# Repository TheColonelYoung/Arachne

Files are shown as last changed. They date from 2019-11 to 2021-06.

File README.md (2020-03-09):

# Project Arachne  
Mainly 3D printed manipulator with 6 axis of freedom based on design of steward platform  

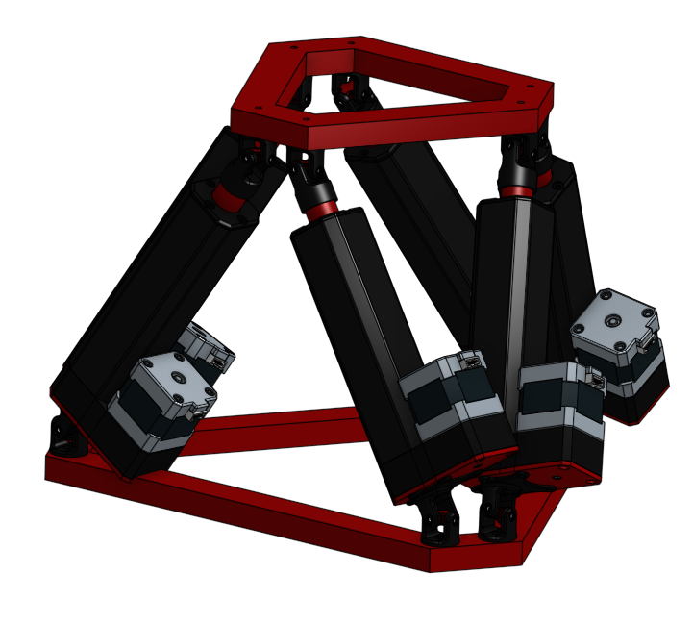
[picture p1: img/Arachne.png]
  

**!!! Now the notes in this repository are rather assumptions that will need to be verified in practice !!!**  

Platform is based on two nearly triangular bases connected with 6 linear actuators.  
Control of these actuators is driven from motherboard.  
Lower base is stationary, upper base part is movable.  
Motherboard is positioned in lower triangle base. Motherboard communicates with controller (pc) via serial line with G-code.  
First version of platform is 3D printed. Next version are supposed to be from aluminium.  

# **Motion system**  
Motion system is based on [affine transformation](https://en.wikipedia.org/wiki/Affine_transformation).  
Basic system contains from seven points. Which are placed in center of platform and in points of connection with actuators.  
Points are on both triangular bases. Corresponding points have same numbers.  
Position of point is described as coordinates in cartesian system.  
Center point is not used for calculation of motion, is used only as center point of mass.  
- Represent zero-point in three-dimensional space  
- Zero point of Z is when platform is set to minimal height (home position)  
- Can probably be used for optimization of speed  
- Center point can be used to determinate unreachable positions (not all) and as center position of object for affine transformations  

Every point is represented as vector [x,y,z,1].  

### Travel distance  
Distance between connect points &nbsp;of actuator on lower and upper bases is calculated.  
- Calculation is based on usage of euclidian distance calculation in three dimensional space  
- $d(a,b) = \sqrt{(a_x - b_x)^2 + (a_y - b_y)^2 + (a_z - b_z)^2}$  

Affine transformation is applied on all point of connection with actuators on upper base.  
Now is calculated new distance between fixed and movable points. Difference between distances in old and new position is travel distance of actuator.  
By repeating this process for every actuator is calculated one move of platform.  
Rotation terms: Pitch(X), Roll(Y), Yaw(Z)  

### Speed  
Speed scaling is linear based on travel distance of actuator.  
Acceleration must grow proportionally as speed.  
Traveled distance is integration of actual speed of motor by time.  
Example: Two motor M1 - travels 10mm, M2 - travels 30mm,  
- Maximal speed is tested (before usage of device) and used for motor with the longest distance (as well as acceleration)  
- M1 use three-times lower speed and acceleration because of travel distance is three-times lower  
- Travel time is same for both motor, so motors cannot jam due to incorrect position  

### Problems  
Jams of platforms are possible when movement is not synchronized. In this state some motor can be in end-position, but motion is not done.  
Main issue is when position of points in unknown. This happens when platform is powered on. Before power of platform must be homed -> this cannot be reliably secured.  
Possible homing sequence is that all actuators will be moved with same speed to their home position. But there is possibility of jam.  

### Example  
This example is calculated only for one actuators, others have same calculations.  
Platform is now at home position. So position of points describes offset from zero point.  
Length of all actuator is same. Probably zero length of pushrods + length of body.  
In this example is body length two times retractable length. Minimal length 30mm, maximal length is 50mm.  
Length is calculated between mates connecting base and actuator.  

Point on upper base ($P_{UP}$) is at `[-2, 0, 0, 1]`, motions are shift forward (Y+2), and rotation to right(Z+90°).  
Point on lower base ($P_{LOW}$) is at `[-1, 2, -2.45, 1]`, Z offset is determinated by vertical distance between lower and upper base in home state.  

**Shift matrix:**  
$\begin{bmatrix}1 & 0 & 0 & X \\0 & 1 & 0 & Y \\ 0 & 0 & 1 & Z \\ 0 & 0 & 0 & 1 \\\end{bmatrix}$  

**Rotation matrix around Z - Yaw($\gamma$):**  
$\begin{bmatrix}\cos(\gamma) & -\sin(\gamma) & 0 & 0 \\\sin(\gamma) & \cos(\gamma) & 0 & 0 \\ 0 & 0 & 1 & 0 \\ 0 & 0 & 0 & 1 \\\end{bmatrix}$  

**Multiplication of matrix**  
Note: if platform is not home is necessary to make another translation of object from current position of center point to center of space. This is represented as empty translation-1 matrix  
[Translation-1 * Rotation * Translation * Point]  

New coordinates of $P_{UP}$ are `[-2, -2, 0, 1]`  

Old distance between $P_{UP}$ and $P_{LOW}$ is: 3.317 cm  
- Calculation: $d = \sqrt{(-2 - -1)^2 + (0 - 2)^2 + (0 - -2.45)^2} = 3.317$  

New distance between $P_{UP}$ and $P_{LOW}$ is: 4.796 cm  
- Calculation: $d = \sqrt{(-2 - -1)^2 + (-2 - 2)^2 + (0 - -2.45)^2} = 4.796$  

Difference between old and new length of actuator is: 1.479 cm  

So actuator must change length to 4.796 cm, which is nearly maximal length (in this example).  
Change of length is + 1.479 cm, speed and acceleration depends on motion of other actuators.  

# **Construction**  

### Joints  
Linear actuators are connected with hexagonal platform with universal joint with can give joint freedom to move freely. Rotation of joint should not be constrained by joint but by length of arm (linear actuator length).  

Joints consists of 3 parts. Two forks and one central block. X and Y axis of forks are perpendicular between forks (forks are turned against self by 90° on Z axis). Fork is connected to central block through small ball bearing. This ball bearing removed as much of friction as possible.  

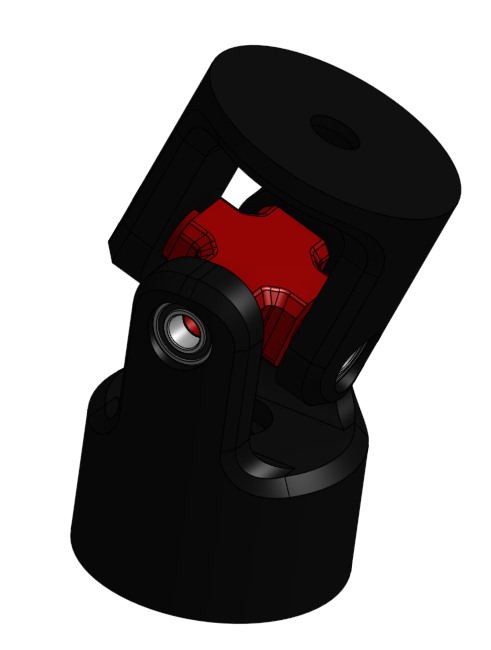
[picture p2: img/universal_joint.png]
Universal joint
  
**Universal joint**  

# **PCB**  
Main Motherboard contains six stepper motor drivers L6470 in TSSOP28 package.  
PCB is designed with maximal dimensions of 10x7cm, so it can be cheaply manufactured.  

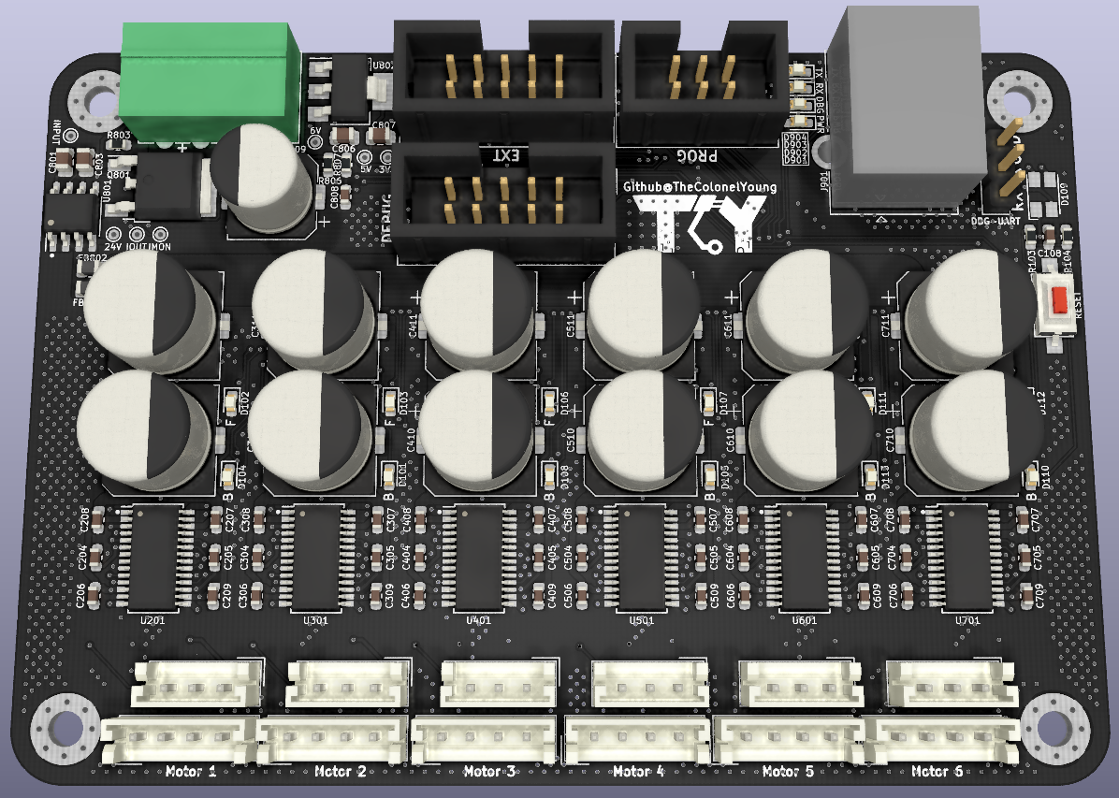
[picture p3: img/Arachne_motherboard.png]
  

### Specifications  
- Maximal input voltage is 36V  
- PCB is designed for maximal current of 8A into motor, this assumes 6x1.2A stepper motors  
- Input stage contains current sensor for monitoring of actual current  
- Stepper motor end position can be detected via driver build-in stall detection or through endstop (one per each stepper)  
    - Endstop should be Normally Open and connect ground to sense pin  
    - Connector contains 3.3V power output for powering some position sensor instead of tactile switch between sense and ground  
- Stepper drivers are in line, so heatsinks can be fit on them  
- Via EXT IDC connector can be connected sensor for motion feedback over SPI or I2C  
- DEBUG connector pinout is compatible with 10-pin IDC Saleae layout  
- Minimal width trace is 5.1 mils (0.13 mm)  
- Minimal drill size id 0.3mm

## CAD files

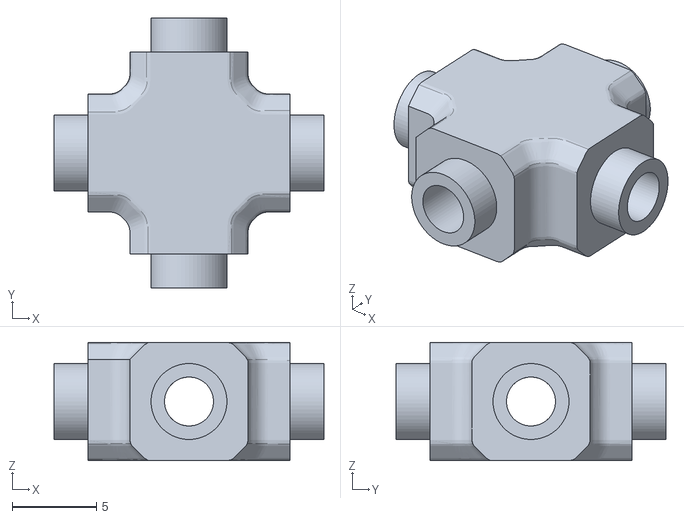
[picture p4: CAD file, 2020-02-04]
STL/Center_block.stl
16.0 x 16.0 x 7.00

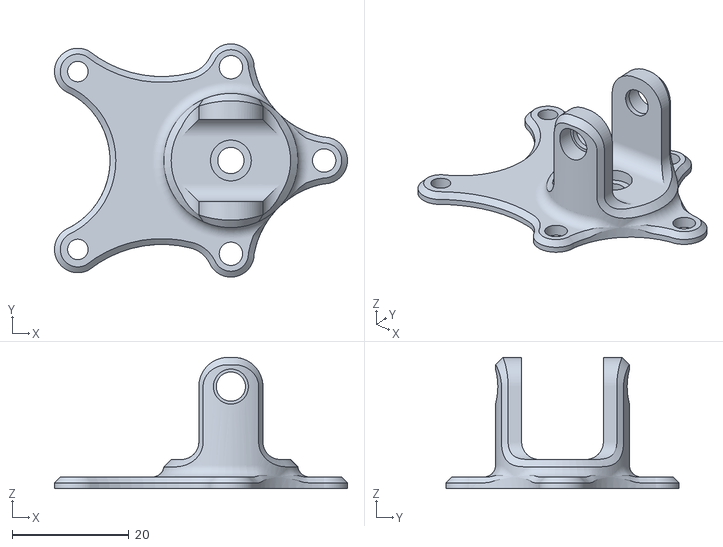
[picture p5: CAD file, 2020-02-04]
STL/Joint_fork_gearbox.stl
50.2 x 40.0 x 22.5

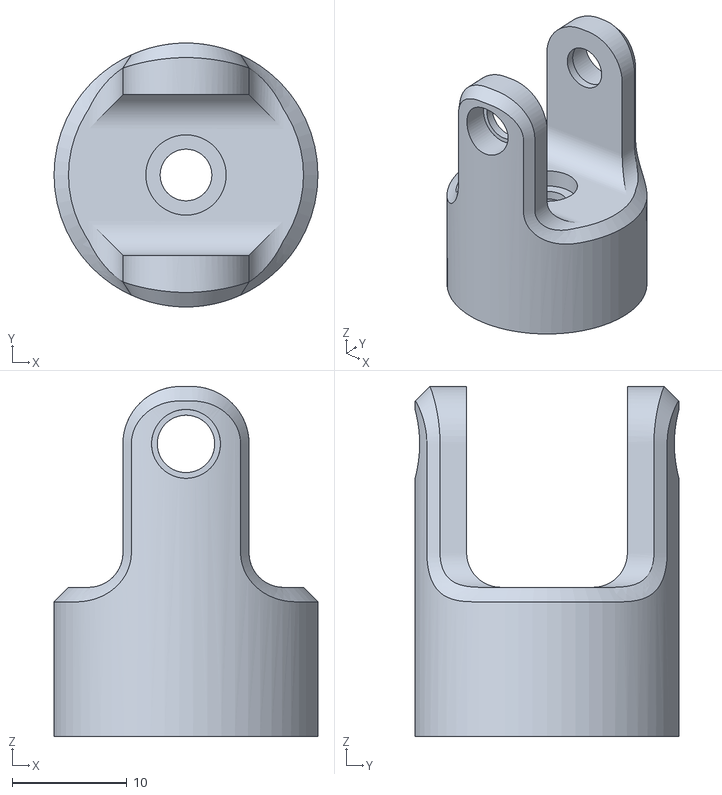
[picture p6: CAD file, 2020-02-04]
STL/Joint_fork_shaft.stl
23.0 x 23.0 x 30.5

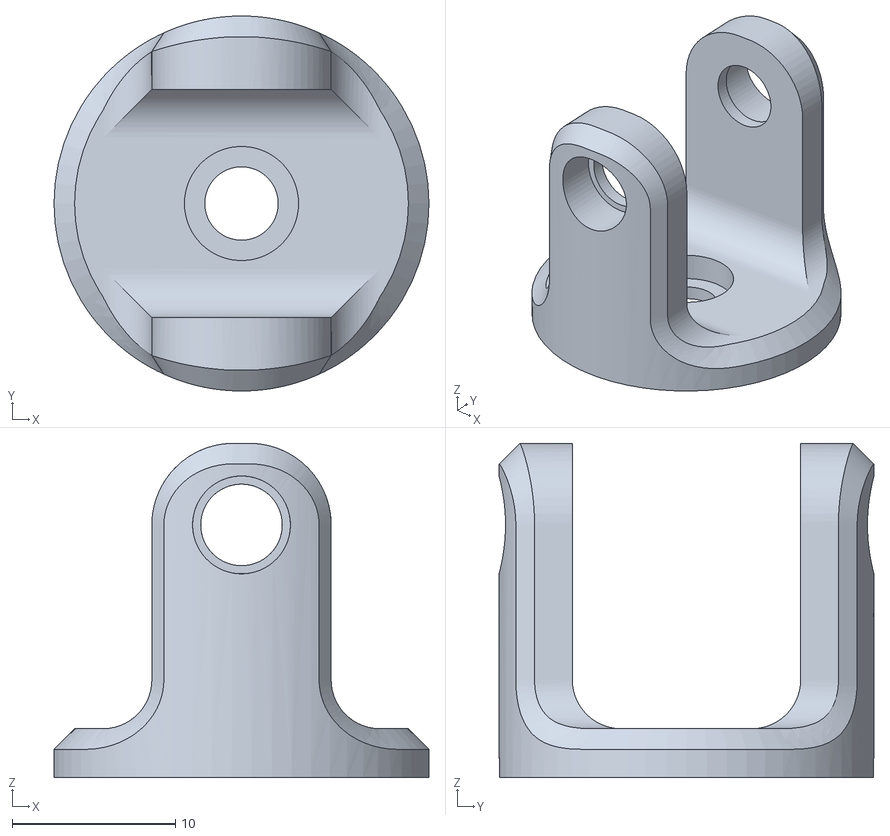
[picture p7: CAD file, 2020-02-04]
STL/Joint_fork_base.stl
23.0 x 23.0 x 20.5

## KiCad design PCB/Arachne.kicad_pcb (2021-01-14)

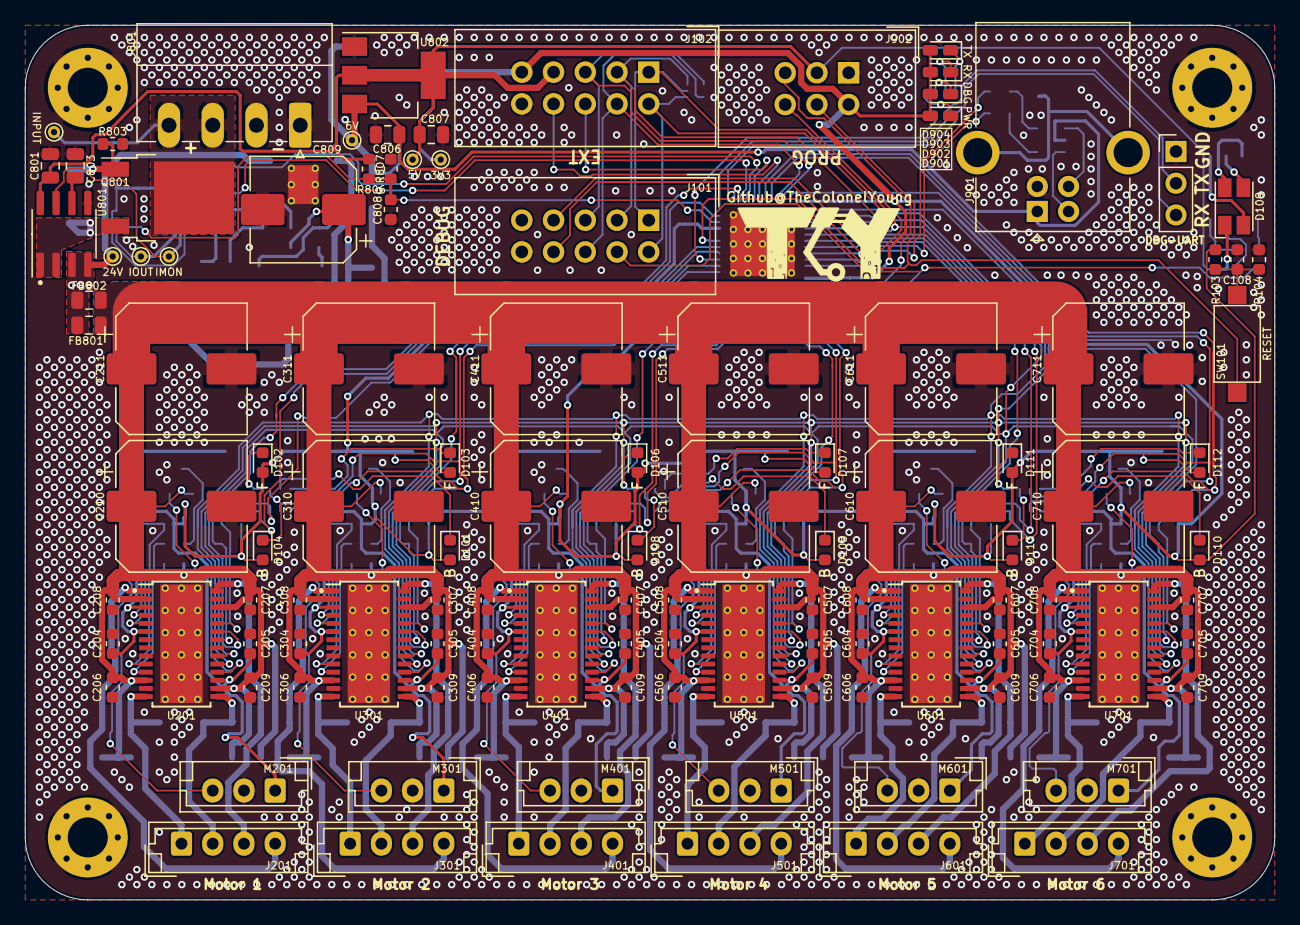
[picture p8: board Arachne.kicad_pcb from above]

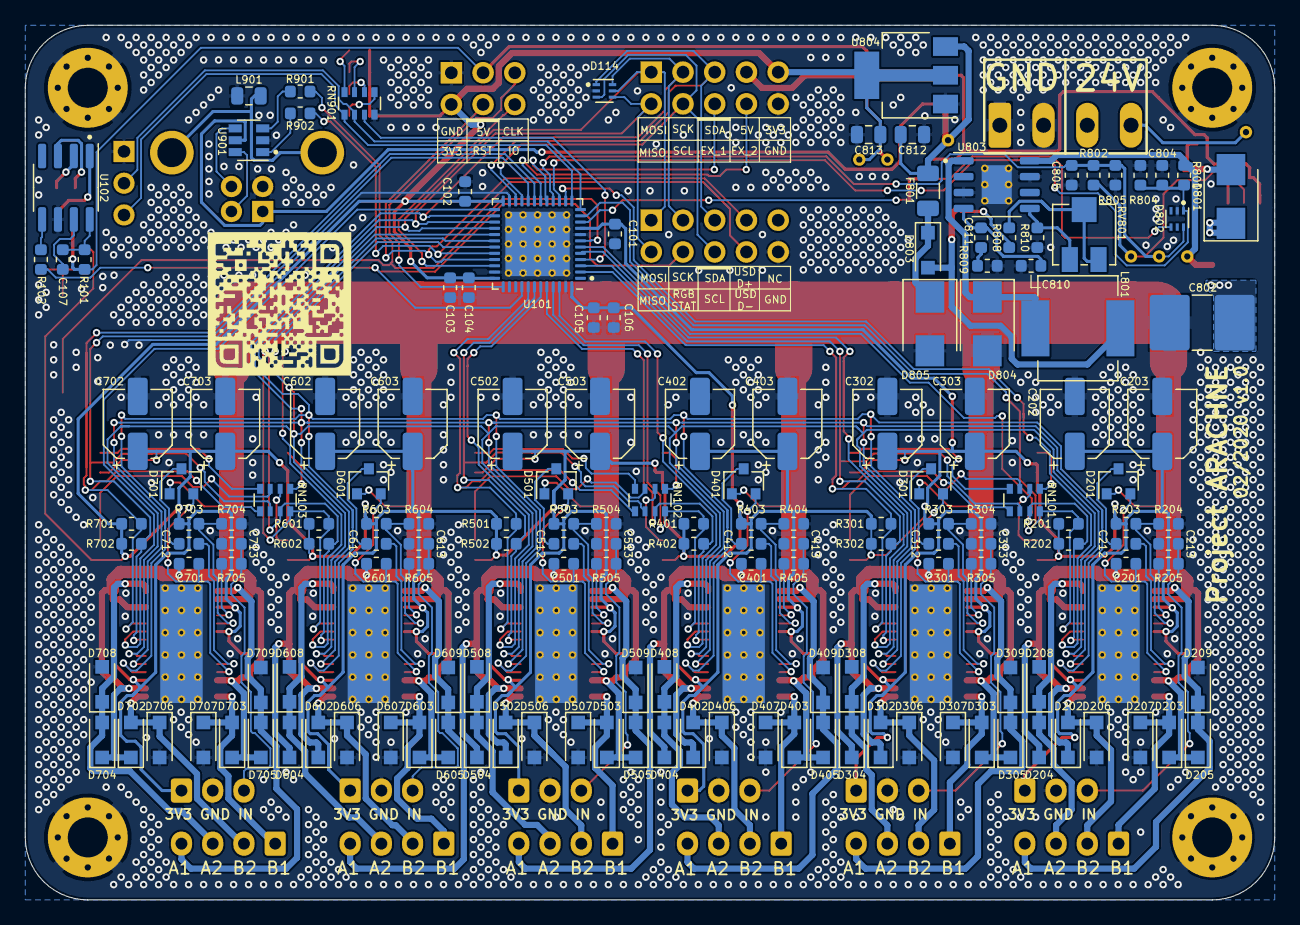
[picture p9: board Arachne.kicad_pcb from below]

Board: 2 copper layers, 100.0 x 70.0 mm, 276 parts (158 on the bottom side), 143 nets.

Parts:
C101, C102, C103, C104, C105, C106, C107, C108, C213, C313, C413, C513, C613, C713, C804, C805, C808: 100nF; C_0603_1608Metric
C201, C301, C401, C501, C601, C701: 220nF/16V; C_0603_1608Metric
C202, C203, C302, C303, C402, C403, C502, C503, C602, C603, C702, C703: 47uF/6,3V; CP_Elec_5x5.3
C204, C205, C206, C207, C208, C209, C304, C305, C306, C307, C308, C309, C404, C405, C406, C407, C408, C409, C504, C505, C506, C507, C508, C509, C604, C605, C606, C607, C608, C609, C704, C705, C706, C707, C708, C709: 100nF/50V; C_0603_1608Metric
C210, C211, C310, C311, C410, C411, C510, C511, C610, C611, C710, C711: 100uF/63V; CP_Elec_10x10
C212, C312, C412, C512, C612, C712: 10nF/50V; C_0603_1608Metric
C801, C803: 1uF (X7R); C_0805_2012Metric
C802: 10uF 50V (ceramic); C_2816_7142Metric_Pad3.20x4.45mm_HandSolder
C806, C807, C812, C813: 4.7uF (X7R); C_0805_2012Metric
C809: 300uF 16V; CP_Elec_8x10
C810: 220nF; C_0603_1608Metric
C811: 22nF; C_0603_1608Metric
D101, D102, D103, D104, D105, D106, D107, D108, D110, D111, D112, D113: LED; LED_0603_1608Metric
D109: ASMB-MTB0-0A3A2; LED_Avago_PLCC4_3.2x2.8mm_CW
D114, D802: ESDA6V1-5SC6; ST_UQFN-6L_1.5x1.7mm_Pitch0.5mm
D201, D301, D401, D501, D601, D701: BAV99; SOT-23
D202, D203, D204, D205, D206, D207, D208, D209, D302, D303, D304, D305, D306, D307, D308, D309, D402, D403, D404, D405, D406, D407, D408, D409, D502, D503, D504, D505, D506, D507, D508, D509, D602, D603, D604, D605, D606, D607, D608, D609, D702, D703, D704, D705, D706, D707, D708, D709, D803: SKL310; D_SOD-123F
D801: 1SMB5925; D_SMB
D804: 7V; D_SMB
D805: STPS340U; D_SMB
D901: GREEN; LED_0603_1608Metric_Castellated
D902: YELLOW; LED_0603_1608Metric_Castellated
D903, D904: BLUE; LED_0603_1608Metric_Castellated
F801: 2A; Fuse_1206_3216Metric
FB801, FB802: 22R@100MHz; L_0805_2012Metric
H101, H102, H103, H104: M3; MountingHole_3.2mm_M3_Pad_Via
J101: Salae_logic; IDC-Header_2x05_P2.54mm_Vertical
J102: Extension; IDC-Header_2x05_P2.54mm_Vertical
J201, J301, J401, J501, J601, J701: SW2; JST_EH_B3B-EH-A_1x03_P2.50mm_Vertical
J801: V_IN; PhoenixContact_MC_1,5_4-G-3.5_1x04_P3.50mm_Horizontal
J901: USB_B; USB_B_OST_USB-B1HSxx_Horizontal
J902: PROG_CONN_STM_6p; IDC-Header_2x03_P2.54mm_Vertical
J903: DBG_UART; PinHeader_1x03_P2.54mm_Vertical
L801: 15uH; L_Neosid_Ms85
L901: 50R@100MHz, 3A; L_0805_2012Metric
M201, M301, M401, M501, M601, M701: Stepper_Motor_bipolar; JST_EH_B4B-EH-A_1x04_P2.50mm_Vertical
Q801: AOD4189; TO-252-2
R101, R102, R901, R902: 22R; R_0603_1608Metric
R103, R201, R202, R301, R302, R401, R402, R501, R502, R601, R602, R701, R702, R803: 100k; R_0603_1608Metric
R104, R802, R804, R805, R806, R807, R810: 10k; R_0603_1608Metric
R203, R303, R403, R503, R603, R703: 560k; R_0603_1608Metric
R204, R304, R404, R504, R604, R704: 2k7; R_0603_1608Metric
R205, R305, R405, R505, R605, R705: 1k; R_0603_1608Metric
R801: 180k; R_0603_1608Metric
R808: 20k; R_0603_1608Metric
R809: 4.7k; R_0603_1608Metric
RN101, RN102, RN103: 4x22R; R_Array_Convex_4x0603
RN901: R_Pack04; R_Array_Convex_4x0603
RV801: 20k; Potentiometer_Bourns_3214J_Horizontal
SW101: SW_Push; SW_SPST_CK_RS282G05A3
TP801: PWR_IN; TestPoint_THTPad_D1.0mm_Drill0.5mm
TP803: I_MAIN; TestPoint_THTPad_D1.0mm_Drill0.5mm
TP804: 24V; TestPoint_THTPad_D1.0mm_Drill0.5mm
TP805: I_DIV; TestPoint_THTPad_D1.0mm_Drill0.5mm
TP806: 5V; TestPoint_THTPad_D1.0mm_Drill0.5mm
TP807: 6V; TestPoint_THTPad_D1.0mm_Drill0.5mm
TP808: 3V3; TestPoint_THTPad_D1.0mm_Drill0.5mm
U101: STM32L452CEUx; QFN-48-1EP_7x7mm_P0.5mm_EP5.15x5.15mm_ThermalVias
U102: WS2818B; SOP-8_3.76x4.96mm_P1.27mm
U201, U301, U401, U501, U601, U701: L6470_HTSSOP28; HTSSOP-28-1EP_4.4x9.7mm_P0.65mm_EP3.4x9.5mm_ThermalVias
U801: ACS712xLCTR-20A; SOIC-8_3.9x4.9mm_P1.27mm
U802: NCP1117-5.0_SOT223; SOT-223-3_TabPin2
U803: L5973D; HSOP-8-1EP_3.9x4.9mm_P1.27mm_EP2.41x3.1mm_ThermalVias
U804: NCP1117-3.3_SOT223; SOT-223-3_TabPin2
U901: USBLC6-2SC6; SOT-23-6

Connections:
+3V3: C101.1, C102.1, C103.1, C104.1, C105.1, C106.1, C202.1, C203.1, C204.1, C205.1, C302.1, C303.1, C304.1, C305.1, C402.1, C403.1, C404.1, C405.1, C502.1, C503.1, C504.1, C505.1, C602.1, C603.1, C604.1, C605.1, C702.1, C703.1, C704.1, C705.1, C813.1, D101.2, D102.2, D103.2, D104.2, D105.2, D106.2, D107.2, D108.2, D110.2, D111.2, D112.2, D113.2, D901.2, D902.2, D903.2, D904.2, J102.9, J201.1, J301.1, J401.1, J501.1, J601.1, J701.1, J902.2, R103.1, R201.1, R202.1, R203.1, R301.1, R302.1, R303.1, R401.1, R402.1, R403.1, R501.1, R502.1, R503.1, R601.1, R602.1, R603.1, R701.1, R702.1, R703.1, TP808.1, U101.9, U101.24, U101.36, U101.48, U201.3, U201.6, U201.17, U301.3, U301.6, U301.17, U401.3, U401.6, U401.17, U501.3, U501.6, U501.17, U601.3, U601.6, U601.17, U701.3, U701.6, U701.17, U804.2
+5V: C801.2, C807.1, D109.1, J102.7, J902.3, R101.1, R806.1, TP806.1, U801.8, U802.2
+24V: C802.1, FB801.2, FB802.2, R801.1, TP804.1, U801.3, U801.4, U803.8
/5V_MON: C808.1, D802.4, R806.2, R807.1, U101.10
/BUSY_1: R202.2, RN101.7, U101.6, U201.22
/BUSY_2: R302.2, RN101.6, U101.3, U301.22
/BUSY_3: R402.2, RN102.7, U101.44, U401.22
/BUSY_4: R502.2, RN102.6, U101.42, U501.22
/BUSY_5: R602.2, RN103.7, U101.30, U601.22
/BUSY_6: R702.2, RN103.6, U101.20, U701.22
/CS_1: U101.14, U201.23
/CS_2: U101.5, U301.23
/CS_3: U101.46, U401.23
/CS_4: U101.43, U501.23
/CS_5: U101.31, U601.23
/CS_6: U101.25, U701.23
/EXT_1: J102.6, U101.17
/EXT_2: J102.8, U101.18
/FLAG_1: R201.2, RN101.8, U101.11, U201.24
/FLAG_2: R301.2, RN101.5, U101.2, U301.24
/FLAG_3: R401.2, RN102.8, U101.45, U401.24
/FLAG_4: R501.2, RN102.5, U101.41, U501.24
/FLAG_5: R601.2, RN103.8, U101.29, U601.24
/FLAG_6: R701.2, RN103.5, U101.19, U701.24
/I2C_SCL: D114.3, J101.6, J102.4, U101.21
/I2C_SDA: D114.1, J101.5, J102.5, U101.22
/I_MON: C805.1, D802.6, R802.2, R805.1, TP805.1, U101.16
/Interface/D+: R901.2, U901.3
/Interface/D-: R902.2, U901.1
/Interface/USB+: J901.3, U901.4
/Interface/USB-: J901.2, U901.6
/Motor_1/SW: R205.2, U201.4
/Motor_2/SW: R305.2, U301.4
/Motor_3/SW: R405.2, U401.4
/Motor_4/SW: R505.2, U501.4
/Motor_5/SW: R605.2, U601.4
/Motor_6/SW: R705.2, U701.4
/PWR_MON: C804.1, D802.1, R801.2, R804.1, U101.15
/RESET: J902.4, SW101.2, U101.7
/RGB_STAT: J101.4, R102.2, U101.40
/SPI_MISO: D114.4, J101.2, J102.2, U101.27, U201.18, U301.18, U401.18, U501.18, U601.18, U701.18
/SPI_MOSI: D114.5, J101.1, J102.1, U101.28, U201.20, U301.20, U401.20, U501.20, U601.20, U701.20
/SPI_SCK: D114.6, J101.3, J102.3, U101.26, U201.19, U301.19, U401.19, U501.19, U601.19, U701.19
/STAT: RN901.7, U101.4
/SWCLK: J902.5, U101.37
/SWDIO: J902.6, U101.34
/UART_2_RX: J903.3, RN901.5, U101.13
/UART_2_TX: J903.2, RN901.6, U101.12
/USB_D+: J101.7, R901.1, U101.33
/USB_D-: J101.8, R902.1, U101.32
GND: C101.2, C102.2, C103.2, C104.2, C105.2, C106.2, C108.2, C202.2, C203.2, C204.2, C205.2, C206.2, C207.2, C208.2, C209.2, C210.2, C211.2, C213.2, C302.2, C303.2, C304.2, C305.2, C306.2, C307.2, C308.2, C309.2, C310.2, C311.2, C313.2, C402.2, C403.2, C404.2, C405.2, C406.2, C407.2, C408.2, C409.2, C410.2, C411.2, C413.2, C502.2, C503.2, C504.2, C505.2, C506.2, C507.2, C508.2, C509.2, C510.2, C511.2, C513.2, C602.2, C603.2, C604.2, C605.2, C606.2, C607.2, C608.2, C609.2, C610.2, C611.2, C613.2, C702.2, C703.2, C704.2, C705.2, C706.2, C707.2, C708.2, C709.2, C710.2, C711.2, C713.2, C801.1, C802.2, C803.2, C804.2, C805.2, C806.2, C807.2, C808.2, C809.2, C810.2, C812.2, C813.2, D114.2, D206.2, D207.2, D208.2, D209.2, D306.2, D307.2, D308.2, D309.2, D406.2, D407.2, D408.2, D409.2, D506.2, D507.2, D508.2, D509.2, D606.2, D607.2, D608.2, D609.2, D706.2, D707.2, D708.2, D709.2, D802.2, D804.2, D805.2, H101.1, H102.1, H103.1, H104.1, J101.10, J102.10, J201.2, J301.2, J401.2, J501.2, J601.2, J701.2, J801.1, J801.2, J901.4, J902.1, J903.1, L901.2, R104.2, R204.2, R304.2, R404.2, R504.2, R604.2, R704.2, R803.2, R804.2, R805.2, R807.2, R809.2, R810.2, RN901.8, U101.8, U101.23, U101.35, U101.47, U101.49, U102.6, U201.9, U201.13, U201.21, U201.27, U201.29, U301.9, U301.13, U301.21, U301.27, U301.29, U401.9, U401.13, U401.21, U401.27, U401.29, U501.9, U501.13, U501.21, U501.27, U501.29, U601.9, U601.13, U601.21, U601.27, U601.29, U701.9, U701.13, U701.21, U701.27, U701.29, U801.5, U802.1, U803.3, U803.7, U803.9, U804.1, U901.2
unnamed: C107.1, R101.2, U102.8
unnamed: C107.2, U102.7
unnamed: C108.1, R103.2, R104.1, SW101.1
unnamed: C201.1, D201.2, U201.11
unnamed: C212.1, D201.3
unnamed: C212.2, U201.10
unnamed: C213.1, J201.3, R205.1
unnamed: C301.1, D301.2, U301.11
unnamed: C312.1, D301.3
unnamed: C312.2, U301.10
unnamed: C313.1, J301.3, R305.1
unnamed: C401.1, D401.2, U401.11
unnamed: C412.1, D401.3
unnamed: C412.2, U401.10
unnamed: C413.1, J401.3, R405.1
unnamed: C501.1, D501.2, U501.11
unnamed: C512.1, D501.3
unnamed: C512.2, U501.10
unnamed: C513.1, J501.3, R505.1
unnamed: C601.1, D601.2, U601.11
unnamed: C612.1, D601.3
unnamed: C612.2, U601.10
unnamed: C613.1, J601.3, R605.1
unnamed: C701.1, D701.2, U701.11
unnamed: C712.1, D701.3
unnamed: C712.2, U701.10
unnamed: C713.1, J701.3, R705.1
unnamed: C803.1, U801.6
unnamed: C809.1, D803.2, L801.2, R808.1
unnamed: C810.1, C811.1, U803.4
unnamed: C811.2, R809.1
unnamed: D101.1, RN101.3
unnamed: D102.1, RN101.1
unnamed: D103.1, RN101.4
unnamed: D104.1, RN101.2
unnamed: D105.1, RN102.3
unnamed: D106.1, RN102.1
unnamed: D107.1, RN102.4
unnamed: D108.1, RN102.2
unnamed: D109.2, U102.3
unnamed: D109.3, U102.2
unnamed: D109.4, U102.1
unnamed: D110.1, RN103.3
unnamed: D111.1, RN103.1
unnamed: D112.1, RN103.4
unnamed: D113.1, RN103.2
unnamed: D202.2, D206.1, M201.2, U201.15
unnamed: D203.2, D207.1, M201.1, U201.14
unnamed: D204.2, D208.1, M201.3, U201.28
unnamed: D205.2, D209.1, M201.4, U201.1
unnamed: D302.2, D306.1, M301.2, U301.15
unnamed: D303.2, D307.1, M301.1, U301.14
unnamed: D304.2, D308.1, M301.3, U301.28
unnamed: D305.2, D309.1, M301.4, U301.1
unnamed: D402.2, D406.1, M401.2, U401.15
unnamed: D403.2, D407.1, M401.1, U401.14
unnamed: D404.2, D408.1, M401.3, U401.28
unnamed: D405.2, D409.1, M401.4, U401.1
unnamed: D502.2, D506.1, M501.2, U501.15
unnamed: D503.2, D507.1, M501.1, U501.14
unnamed: D504.2, D508.1, M501.3, U501.28
unnamed: D505.2, D509.1, M501.4, U501.1
unnamed: D602.2, D606.1, M601.2, U601.15
unnamed: D603.2, D607.1, M601.1, U601.14
unnamed: D604.2, D608.1, M601.3, U601.28
unnamed: D605.2, D609.1, M601.4, U601.1
unnamed: D702.2, D706.1, M701.2, U701.15
unnamed: D703.2, D707.1, M701.1, U701.14
unnamed: D704.2, D708.1, M701.3, U701.28
unnamed: D705.2, D709.1, M701.4, U701.1
unnamed: D801.1, Q801.3, U801.1, U801.2
unnamed: D801.2, Q801.1, R803.1
unnamed: D803.1, D804.1, F801.2
unnamed: D805.1, L801.1, U803.1
unnamed: D901.1, RN901.1
unnamed: D902.1, RN901.2
unnamed: D903.1, RN901.3
unnamed: D904.1, RN901.4
unnamed: J801.3, J801.4, Q801.2, TP801.1
unnamed: J901.5, L901.1
unnamed: R102.1, U102.5
unnamed: R203.2, R204.1, U201.5
unnamed: R303.2, R304.1, U301.5
unnamed: R403.2, R404.1, U401.5
unnamed: R503.2, R504.1, U501.5
unnamed: R603.2, R604.1, U601.5
unnamed: R703.2, R704.1, U701.5
unnamed: R802.1, TP803.1, U801.7
unnamed: R808.2, RV801.1, RV801.2
unnamed: R810.1, RV801.3, U803.5
USB_VCC: C806.1, C812.1, F801.1, J901.1, TP807.1, U802.3, U804.3, U901.5
VMOT: C201.2, C206.1, C207.1, C208.1, C209.1, C210.1, C211.1, C301.2, C306.1, C307.1, C308.1, C309.1, C310.1, C311.1, C401.2, C406.1, C407.1, C408.1, C409.1, C410.1, C411.1, C501.2, C506.1, C507.1, C508.1, C509.1, C510.1, C511.1, C601.2, C606.1, C607.1, C608.1, C609.1, C610.1, C611.1, C701.2, C706.1, C707.1, C708.1, C709.1, C710.1, C711.1, D201.1, D202.1, D203.1, D204.1, D205.1, D301.1, D302.1, D303.1, D304.1, D305.1, D401.1, D402.1, D403.1, D404.1, D405.1, D501.1, D502.1, D503.1, D504.1, D505.1, D601.1, D602.1, D603.1, D604.1, D605.1, D701.1, D702.1, D703.1, D704.1, D705.1, FB801.1, FB802.1, U201.2, U201.12, U201.16, U201.26, U301.2, U301.12, U301.16, U301.26, U401.2, U401.12, U401.16, U401.26, U501.2, U501.12, U501.16, U501.26, U601.2, U601.12, U601.16, U601.26, U701.2, U701.12, U701.16, U701.26

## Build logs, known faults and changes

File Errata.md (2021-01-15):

# V1.0

## Hardware

- Diode should be added to USB power line
    - Without diode USB-LC6 will be damaged
    - Also without diode voltage from step-down regulator can get to USB power line (power line overvoltage)
    - Can be fixed by adding low dropout shottky diode to USB_VCC line

- Motor connector are bit wider then footprint
    - Connectors for motors a endstops are overlapping
    - Can be fixed by sanding off 0.5mm of material from back side of endstops connector (after that fits perfectly)

- Motor input voltage drop compensation is connection to 3.3V instead of VMOT
    - Compensation cannot be utilized

- Transil in stepdown regulator should be placed after fuse not before
    - When transil opens is triggered overcurrent protection of stepdow
    - Fuse is not activated by transil

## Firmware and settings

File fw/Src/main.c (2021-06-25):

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
/* Includes ------------------------------------------------------------------*/
#include "main.h"
#include "cmsis_os.h"
#include "usb_device.h"

/* USER CODE BEGIN Includes */
#include <functional>

#include "gpio/pin.hpp"
#include "device/device.hpp"
#include "usbd_cdc_if.h"
#include "misc/logger.hpp"
#include "misc/invocation_wrapper.hpp"
#include "tools/tasker.hpp"
#include "led/WS2818B.hpp"
#include "motor/L6470.hpp"
#include "construction/motion_axis_L6470.hpp"
#include "../app/eyrina.hpp"
/* USER CODE END Includes */

ADC_HandleTypeDef hadc1;

I2C_HandleTypeDef hi2c2;

SPI_HandleTypeDef hspi2;

TIM_HandleTypeDef htim2;
TIM_HandleTypeDef htim3;
DMA_HandleTypeDef hdma_tim3_ch1_trig;

UART_HandleTypeDef huart2;

/* Definitions for Hearth_beat */
osThreadId_t Hearth_beatHandle;
const osThreadAttr_t Hearth_beat_attributes = {
    .name       = "Hearth_beat",
    .stack_size = 128 * 4,
    .priority   = (osPriority_t) osPriorityLow,
};
void SystemClock_Config(void);
static void MX_GPIO_Init(void);
static void MX_DMA_Init(void);
static void MX_ADC1_Init(void);
static void MX_SPI2_Init(void);
static void MX_TIM3_Init(void);
static void MX_USART2_UART_Init(void);
static void MX_I2C2_Init(void);
static void MX_TIM2_Init(void);
void Hearth_beat_enter(void *argument);

/**
  * @brief  The application entry point.
  * @retval int
  */
int main(void){
    /* MCU Configuration--------------------------------------------------------*/

    /* Reset of all peripherals, Initializes the Flash interface and the Systick. */
    HAL_Init();

    /* Configure the system clock */
    SystemClock_Config();

    /* Initialize all configured peripherals */
    MX_GPIO_Init();
    MX_DMA_Init();
    MX_ADC1_Init();
    MX_SPI2_Init();
    MX_TIM3_Init();
    MX_USART2_UART_Init();
    MX_I2C2_Init();
    MX_TIM2_Init();
    /* Init scheduler */
    osKernelInitialize();

    /* USER CODE BEGIN RTOS_MUTEX */
    /* add mutexes, ... */
    /* USER CODE END RTOS_MUTEX */

    /* USER CODE BEGIN RTOS_SEMAPHORES */
    /* add semaphores, ... */
    /* USER CODE END RTOS_SEMAPHORES */

    /* USER CODE BEGIN RTOS_TIMERS */
    /* start timers, add new ones, ... */
    /* USER CODE END RTOS_TIMERS */

    /* USER CODE BEGIN RTOS_QUEUES */
    /* add queues, ... */
    /* USER CODE END RTOS_QUEUES */

    /* Create the thread(s) */
    /* creation of Hearth_beat */
    Hearth_beatHandle = osThreadNew(Hearth_beat_enter, NULL, &Hearth_beat_attributes);

    /* USER CODE BEGIN RTOS_THREADS */
    device()->Enable_CLI(device()->mcu->USB_port);
    device()->Enable_Filesystem();
    device()->cli->Enable_filesystem_executable(device()->fs);
    device()->cli->Enable_history(5);

    Logger().Instance()->Add_log_channel(new Invocation_wrapper<UART, int, string>(device()->mcu->UART_2, &UART::Send));

    Pin *Status_LED = new Pin('C', 15);
    Status_LED->Set(0);

    Tasker::Instance(device()->mcu->TIM_2);
    Tasker::Instance()->New_event(50000, -1, Status_LED, &Pin::Toggle, 0, "LED_Toggle");

    // WS2818B *led = new WS2818B(device()->mcu->TIM_3, 0);
    // led->Color(0x08, 0x00, 0x00);

    // HAL_Delay(100);

    Eyrina *eyrina = new Eyrina();
    eyrina->Init();
    device()->cli->Start_foreground_application("/apps/eyrina");
    /* add threads, ... */
    /* USER CODE END RTOS_THREADS */

    /* USER CODE BEGIN RTOS_EVENTS */
    /* add events, ... */
    /* USER CODE END RTOS_EVENTS */

    /* Start scheduler */
    osKernelStart();

    /* We should never get here as control is now taken by the scheduler */
    /* Infinite loop */
    /* USER CODE BEGIN WHILE */
    while (1) {
        /* USER CODE END WHILE */

        /* USER CODE BEGIN 3 */
    }
    /* USER CODE END 3 */
} // main

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
/* USER CODE BEGIN Header_Hearth_beat_enter */

/**
  * @brief  Function implementing the Hearth_beat thread.
  * @param  argument: Not used
  * @retval None
  */
/* USER CODE END Header_Hearth_beat_enter */
void Hearth_beat_enter(void *argument){
    /* init code for USB_DEVICE */
    MX_USB_DEVICE_Init();
    /* USER CODE BEGIN 5 */
    Pin *Status_LED = new Pin('C', 15);
    Status_LED->Set(0);
    /* Infinite loop */
    for (;;) {
        Status_LED->Set(1);
        osDelay(100);
        Status_LED->Set(0);
        osDelay(100);
    }
    /* USER CODE END 5 */
}

/**
 * @brief  Period elapsed callback in non blocking mode
 * @note   This function is called  when TIM16 interrupt took place, inside
 * HAL_TIM_IRQHandler(). It makes a direct call to HAL_IncTick() to increment
 * a global variable "uwTick" used as application time base.
 * @param  htim : TIM handle
 * @retval None
 */
void HAL_TIM_PeriodElapsedCallback(TIM_HandleTypeDef *htim){
    if (htim->Instance == TIM16) {
        HAL_IncTick();
    }
}

/**
  * @brief  This function is executed in case of error occurrence.
  * @retval None
  */
void Error_Handler(void){
    /* USER CODE BEGIN Error_Handler_Debug */
    /* User can add his own implementation to report the HAL error return state */

    /* USER CODE END Error_Handler_Debug */
}

#ifdef  USE_FULL_ASSERT

/**
  * @brief  Reports the name of the source file and the source line number
  *         where the assert_param error has occurred.
  * @param  file: pointer to the source file name
  * @param  line: assert_param error line source number
  * @retval None
  */
void assert_failed(uint8_t *file, uint32_t line){
    /* USER CODE BEGIN 6 */

    /* User can add his own implementation to report the file name and line number,
       tex: printf("Wrong parameters value: file %s on line %d\r\n", file, line) */
    /* USER CODE END 6 */
}

#endif /* USE_FULL_ASSERT */

/************************ (C) COPYRIGHT STMicroelectronics *****END OF FILE****/

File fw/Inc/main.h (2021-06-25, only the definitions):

#define FLAG_2_Pin GPIO_PIN_13
#define FLAG_2_GPIO_Port GPIOC
#define BUSY_2_Pin GPIO_PIN_14
#define BUSY_2_GPIO_Port GPIOC
#define STAT_Pin GPIO_PIN_15
#define STAT_GPIO_Port GPIOC
#define CS_2_Pin GPIO_PIN_0
#define CS_2_GPIO_Port GPIOH
#define BUSY_1_Pin GPIO_PIN_1
#define BUSY_1_GPIO_Port GPIOH
#define BUSY_1_EXTI_IRQn EXTI1_IRQn
#define _5V_MON_Pin GPIO_PIN_0
#define _5V_MON_GPIO_Port GPIOA
#define FLAG_1_Pin GPIO_PIN_1
#define FLAG_1_GPIO_Port GPIOA
#define CS_1_Pin GPIO_PIN_4
#define CS_1_GPIO_Port GPIOA
#define PWM_MON_Pin GPIO_PIN_5
#define PWM_MON_GPIO_Port GPIOA
#define I_MON_Pin GPIO_PIN_6
#define I_MON_GPIO_Port GPIOA
#define EXT_1_Pin GPIO_PIN_7
#define EXT_1_GPIO_Port GPIOA
#define EXT_2_Pin GPIO_PIN_0
#define EXT_2_GPIO_Port GPIOB
#define FLAG_6_Pin GPIO_PIN_1
#define FLAG_6_GPIO_Port GPIOB
#define BUSY_6_Pin GPIO_PIN_2
#define BUSY_6_GPIO_Port GPIOB
#define CS_6_Pin GPIO_PIN_12
#define CS_6_GPIO_Port GPIOB
#define FLAG_5_Pin GPIO_PIN_8
#define FLAG_5_GPIO_Port GPIOA
#define BUSY_5_Pin GPIO_PIN_9
#define BUSY_5_GPIO_Port GPIOA
#define CS_5_Pin GPIO_PIN_10
#define CS_5_GPIO_Port GPIOA
#define RGB_STAT_Pin GPIO_PIN_4
#define RGB_STAT_GPIO_Port GPIOB
#define FLAG_4_Pin GPIO_PIN_5
#define FLAG_4_GPIO_Port GPIOB
#define BUSY_4_Pin GPIO_PIN_6
#define BUSY_4_GPIO_Port GPIOB
#define CS_4_Pin GPIO_PIN_7
#define CS_4_GPIO_Port GPIOB
#define BUSY_3_Pin GPIO_PIN_3
#define BUSY_3_GPIO_Port GPIOH
#define FLAG_3_Pin GPIO_PIN_8
#define FLAG_3_GPIO_Port GPIOB
#define CS_3_Pin GPIO_PIN_9
#define CS_3_GPIO_Port GPIOB

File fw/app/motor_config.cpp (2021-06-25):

#include "motor_config.hpp"

namespace Eyrina_config {
const std::array<axis_config, 8> axis_configurations{ {
    { .fullstep_movement = 0.005,
      .axis_name         = 'H',
      .homing_direction  = Motion_axis::Direction::Forward,
      .min_position      = 0, // - 0.5
      .max_position      = 0.5,
      .homing_speed      = 0.5 }
} };

const std::array<motor_config, 8> motor_configurations
{ {
    // Motor_8 - H
    {
        .supply_voltage         = 24.0,
        .target_current         = 1.0,
        .coil_impedance         = 4.2,
        .coil_inductance        = 7.2,
        .electric_constant      = 0.068,
        .microsteps             = 128,
        .acceleration           = 1000,
        .deceleration           = 2000,
        .min_speed              = 100,
        .max_speed              = 1200,
        .overcurrent            = 2400,
        .stall_current          = 800,
        .fullstep_optimization  = 400,
        .low_speed_optimization = true
    }
} };
};

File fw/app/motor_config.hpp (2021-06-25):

/**
 * @file motor_config.hpp
 * @author Petr Malaník (TheColonelYoung(at)gmail(dot)com)
 * @brief
 * @version 0.1
 * @date 19.05.2021
 */

#include <array>

#include "construction/motion_axis.hpp"

namespace Eyrina_config {
struct motor_config {
    float        supply_voltage    = 36;
    float        target_current    = 1.0;
    float        coil_impedance    = 4.0;
    float        coil_inductance   = 4.0;
    float        electric_constant = 0.05;

    unsigned int microsteps   = 128;
    unsigned int acceleration = 100;
    unsigned int deceleration = 100;

    unsigned int min_speed = 20;
    unsigned int max_speed = 100;

    unsigned int overcurrent   = 1600;
    unsigned int stall_current = 1200;

    unsigned int fullstep_optimization  = 0;
    bool         low_speed_optimization = false;
};

extern const std::array<motor_config, 8> motor_configurations;

struct axis_config {
    double                  fullstep_movement;
    char                   axis_name;
    Motion_axis::Direction homing_direction = Motion_axis::Direction::Forward;
    double                    min_position = 0;
    double                    max_position = 0;
    double                    homing_speed = 0;
};

extern const std::array<axis_config, 8> axis_configurations;
};

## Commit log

2019-07-16 Initialization of Kicad project, update of description
    [Arachne.kicad_pcb, Arachne.sch]
2019-07-27 PCB-Schema: Initialization of project
    First sketch of power input and motor driver IC.
    [Arachne.sch, Motor.sch, Power_old.sch]
2019-07-27 PCB-Schema: Update of labels in power input
    [Arachne.sch, Motor.sch, power.sch]
2019-08-05 Schema: add other motors and create SPI connection
    [Arachne.sch, Motor.sch, power.sch]
2019-08-05 Notes: create PCB section with specifications
2019-11-08 img: add image of universal joint
2019-11-08 Notes: add part about connection of arm to platform (universal joint)
2020-02-04 Notes: image of Onshape assembly add to notes
2020-02-04 STL: add upper universal joint parts
    [Center_block.stl, Joint_fork_base.stl, Joint_fork_shaft.stl]
2020-02-04 STL: add universal joint for lower side of platform which connects to gearbox of arm
    [Joint_fork_gearbox.stl]
2020-02-04 Add gitignore for bak files generated by Kicad
2020-02-04 Schema: add Interface schema, remove old mcu, add divider to current measuring
    [Arachne.sch, Interface.sch, Motor.sch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]
2020-02-04 Schema: add mcu, RGB LED signalization, reset circuit
    [Arachne.sch, Interface.sch, Motor.sch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]
2020-02-04 Schema: add FLAG and BUSY LED signalization, fix driver ground connection
    [Arachne.sch, Interface.sch, Motor.sch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]
2020-02-04 Schema: new part annotation, package assignment
    [Arachne.sch, Interface.sch, Motor.sch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]
2020-02-05 PCB: create basic PB layout, add netlist
    [Arachne.kicad_pcb, Motor.sch]
2020-02-05 PCB: component sorting, add driver space marks to comment layer
    [Arachne.kicad_pcb]
2020-02-06 PCB: routing of first part of stepper motor driver
    [Arachne.kicad_pcb, Arachne.sch, Motor.sch]
2020-02-09 PCB: driver layout optimization, connect caps, connect endstop
    [Arachne.kicad_pcb]
2020-02-09 Schema: fix schema ERC, connect CS, FLAG and BUSY pins to MCU, connect SPI
    ERC: fixed L6470 pin types, add power flags, fixed programming
    connector pin types
    [Arachne.sch, Motor.sch, power.sch]
2020-02-09 PCB: route CS track of 6th driver, optimize layout of driver, connect GND
    [Arachne.kicad_pcb]
2020-02-09 PCB: position labels in silkscreen for driver 6
    [Arachne.kicad_pcb]
2020-02-09 PCB: route driver number 5 (layout replication of 6 with modifications)
    [Arachne.kicad_pcb]
2020-02-10 PCB: add routing of remaining driver (1-4)
    [Arachne.kicad_pcb]
2020-02-10 Schema&PCB: shrink board to 80x100mm, remove excessive mounting holes
    [Arachne.kicad_pcb, Arachne.sch, Motor.sch]
2020-02-10 Schema: swap resistor net input for FLAG and BUSY signalization
    [Arachne.sch, Motor.sch]
2020-02-10 PCB: route bus between drivers, place resistor nets
    [Arachne.kicad_pcb]
2020-02-10 PCB: update VMOT traces to 1 class wider variant
    [Arachne.kicad_pcb]
2020-02-10 PCB: route current meter, reverse polarity protection, stepdown converter
    [Arachne.kicad_pcb, Motor.sch, power.sch]
2020-02-11 PCB: upgrade power lines for VMOT (3mm -> 5mm), add second ferrite to VMOT
    [Arachne.kicad_pcb, power.sch]
2020-02-12 PCB: create new layout for power supply, route LED signalization and reset
    [Arachne.kicad_pcb, Motor.sch, power.sch]
2020-02-12 PCB: routing of linear regulators, enhance ground connection (power supply)
    [Arachne.kicad_pcb]
2020-02-12 Schema: add Salae debug IDC connector
    [Arachne.sch]
2020-02-12 PCB: change programing and debugging IDC connectors to vertical version
    [Arachne.kicad_pcb, Arachne.sch, Interface.sch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]
2020-02-12 PCB: change package size of USB ferrite from 1206 to 0803
    [Arachne.kicad_pcb, Interface.sch, Motor.sch]
2020-02-25 FW: project initialization, I/O pin setup
2020-02-25 FW: add I2C setup in CubeMX
2020-02-25 Schema: Swap pins for L6470 control on MCU
    [Arachne.sch]
2020-02-26 Schema & PCB: add routing of MCu connection, debug and extension port
    [Arachne.kicad_pcb, Arachne.sch, Interface.sch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]
2020-02-26 FW: add pins to CubeMX for I2C and extension connector
2020-02-26 PCB: add ground via stitching, fix unconnected items
    [Arachne.kicad_pcb]
2020-02-26 PCB: add info labels to silkscreen
    [Arachne.kicad_pcb]
2020-03-01 project: add gerbers/ folder to gitignore
2020-03-01 PCB: fix labels for IDC connectors, add polarity signs to main power conn
    [Arachne.kicad_pcb]
2020-03-02 PCB: add labels to BUSY and FLAG LED of stepper motor drivers
    [Arachne.kicad_pcb]
2020-03-02 img: add render of arachne motherboard from KiCAD
2020-03-02 PCB: fix rotation of connector labels
    [Arachne.kicad_pcb]
2020-03-08 PCB: change minimal drill size to 0.3mm (original was 0.2)
    [Arachne.kicad_pcb]
2020-03-09 Notes: update PCB description
2021-01-14 fixup! FW: project cleanup
    [Arachne.ioc, main.c, main.h]
2021-01-14 PCB: update project to kicad nightly 5.99
    [Arachne.kicad_pcb, Arachne.kicad_sch, Interface.kicad_sch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]
2021-05-11 FW: enable SPI for L6470 and Timer_3 for WS2818
2021-05-11 FW: add communication with motor, logging and LED signaling
2021-06-25 Application: integration of eyrina G-code parser and FreeRTOS into device

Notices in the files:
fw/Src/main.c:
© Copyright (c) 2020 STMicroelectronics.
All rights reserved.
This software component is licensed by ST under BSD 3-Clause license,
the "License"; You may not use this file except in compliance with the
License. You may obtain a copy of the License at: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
